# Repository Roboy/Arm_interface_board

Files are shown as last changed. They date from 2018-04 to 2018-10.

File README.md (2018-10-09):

# Arm_interface_board
Board containing all the control units and power distribution for the servos in the arms.

## Hardware Setup
1. Check and/or solder the clock crystal on the board. Bridge the appropiate pads in order to enable it or make use
  of the extra two pins.
2. Crimp the connectors for power/i2c and the servos according to the following diagram:
   - **Power/I2C:**\
      5V |||||| GND         ]\
      SDA|||||| blah        ] TODO
   - **Servos:**\
      The connectors on the board are designed to receive a connection that starting with the indexing pin on the left
      (to the right) look like this:
      - 5V
      - GND
      - SIGNAL\

   Be careful and rearrange the connections before crimping if needed. Also make sure the cables exit the connector in an
   appropiate direction, to avoid loops.

## Software and flashing guide
The board can be programmed with the Arduino IDE but some setup is required.
### For boards with the ATMEGA328PB
This is partially the result of a mistake in ordering the uControllers,
so the board is not actually designed to fit the chip. Even so it works without
much modifications, although one should exercise special care to **tristate** the pins
that are connected directly to power (A & B).
#### Prerequisites
- MCUdude's [MiniCore](https://github.com/MCUdude/MiniCore) (and all it's dependencies:)
- Arduino IDE v.1.6.4 or greater
#### Setup
You need to install extra packages to enable compatibility with this chip in
the Arduino IDE.\
Add the following URLs to the **Additional Boards Manager URLs**:
```
https://mcudude.github.io/MiniCore/package_MCUdude_MiniCore_index.json
```
This one enables and advanced bootloader and the extra functions in the PB series.
For this you also need the latest AVR toolchain (version 1.6.206). Add:
```
https://downloads.arduino.cc/packages/package_avr_3.6.0_index.json
```
to your Boards Manager.\

After you do this you can install the Minicore and update the Arduino AVR boards to
1.6.207 (AVR toolchain).
#### Flashing
To flash the board you need to use an ISP programmer. The easiest way is to use
an arduino as the programmer. You can do this by flashing any Arduino board with
the code from *Examples*>*11. ArduinoISP*>*ArduinoISP*. Afterwards you can select
the AVR chip from the Minicore boards and configure it for the specified clock, etc.
With all options set you can burn the bootloader by selecting "Arduino as ISP"
in the Programmer window.\

Sadly with this version of the AVR toolchain, for some reason the flashing does not work out of the box.
You require the latest version of **avrdude**, and the only way is by compiling
it from the [source](https://github.com/sigmike/avrdude).\
After you install it the flashing procedure is a bit different. You have to first
compile your code, and then using your freshly built avrdude version upload it
to your board.

UPDATE: downgrade to avr boards 1.6.23 and install arduino isp on atmega 2560. switch to 1.6.207 and install bootloader.

sudo ./avrdude -Cavrdude.conf -v -pm328p -cstk500v1 -P/dev/ttyACM0 -b19200 -D -Uflash:w:/tmp/arduino_build_XXXXXX/roboy_arm_board.ino.hex:i -F

in above command replace XXXXXX with your build number

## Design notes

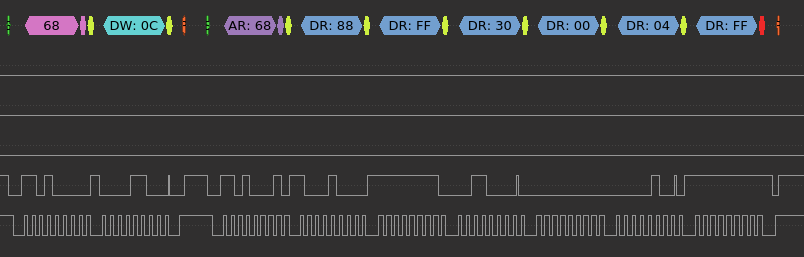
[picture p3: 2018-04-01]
roboy_arm_board/bmi160_IMU/i2cTrace.png

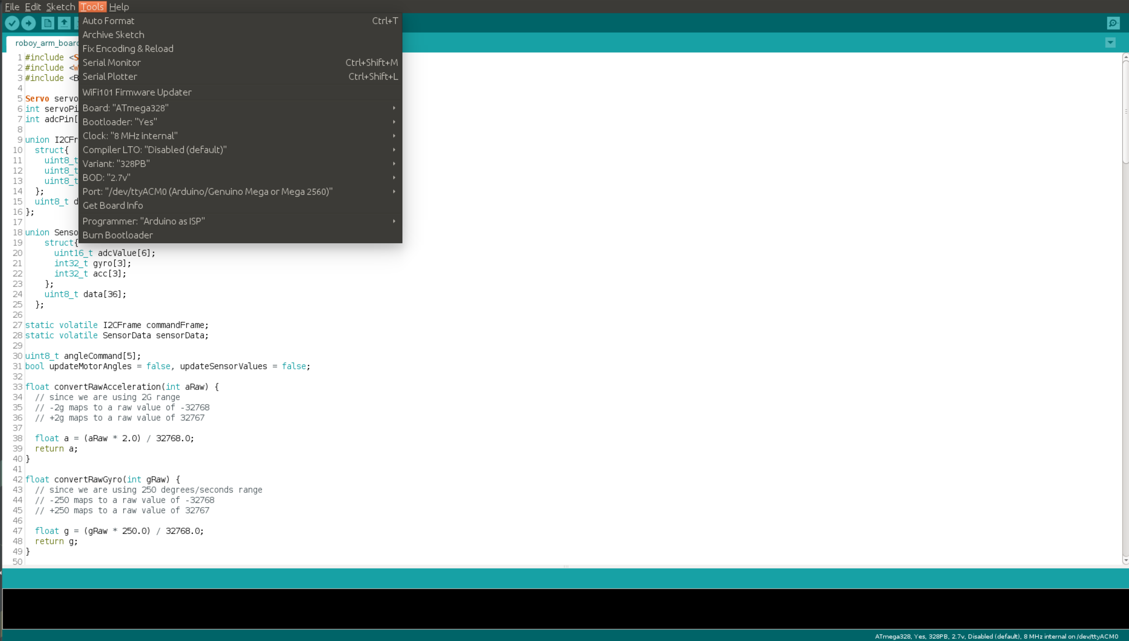
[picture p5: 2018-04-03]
roboy_arm_board/ArduinoConfigsForFlashingArmBoards.png

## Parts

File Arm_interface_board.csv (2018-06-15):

Id | Designator | Package | Quantity | Designation | Supplier and ref
1 | SW2 | SW_SPST_KXT3 | 1 | USER_SW
2 | MK3,MK2,MK1 | MountingHole_2.2mm_M2_DIN965_Pad | 3 | Mounting_Hole_PAD
3 | J19,J18,J16,J17,J20 | TE-Connectivity_Micro-Match_connector_02x02_Pitch_1.27mm | 5 | CONN_01X04
4 | J3 | PinHeader_2x03_P2.54mm_Vertical | 1 | ICSP
5 | U4 | TQFP-32_7x7mm_P0.8mm | 1 | ATMEGA328PB-AU
6 | Y1 | Crystal_SMD_TXC_7M-4Pin_3.2x2.5mm | 1 | TSX-3225 20MHz
7 | J6 | JST_S10B-PHDSS_2x05x2.00mm_Angled | 1 | JST_PHD_connector_02x05_angled_male
8 | C1,C3,C8,C9,C10,C11,C12,C13,C14,C15,C16 | C_0402_1005Metric | 11 | 100n
9 | C4,C5 | C_0402_1005Metric | 2 | 22p
10 | C6,C7 | C_0402_1005Metric | 2 | 1u
11 | S-IN1,Aref1,S1,S2,S3,S4,S5 | TestPoint_Pad_D1.0mm | 7 | TEST_1P
12 | JP1 | SolderJumper-3_P1.3mm_Open_RoundedPad1.0x1.5mm | 1 | XTAL_EN1
13 | JP2 | SolderJumper-3_P1.3mm_Open_RoundedPad1.0x1.5mm | 1 | XTAL_EN2
14 | R2,R9 | R_0402_1005Metric | 2 | 10k
15 | R3,R4,R5,R6,R7 | R_1206_3216Metric | 5 | 10mOhm
16 | SW1 | SW_SPST_SKQG | 1 | SW_Push
17 | U1,U7,U8,U9,U10,U11 | SOT-23-5 | 6 | INA180
18 | U3 | X2SON-8_1.4x1mm_P0.35mm | 1 | NTS0102
19 | U5 | SOT-23-5 | 1 | MIC5504-3.3YM5
20 | U2 | Bosch_LGA-14_3x2.5mm_P0.5mm | 1 | BMI160
21 | R1 | R_1206_3216Metric | 1 | 1mOhm
22 | C2 | CP_Elec_4x5.3 | 1 | 22u
23 | G*** | R1_face_mask_5.5mm | 1 | LOGO
24 | G*** | R1_eyes_mask_5.5mm | 1 | LOGO
25 | G*** | R1_ear_silk_5.5mm | 1 | LOGO
26 | D1 | LED_0603_1608Metric | 1 | LED
27 | R8 | R_0402_1005Metric | 1 | 1k
28 | G*** | Roboy_text_5.5mm | 1 | LOGO
29 | D2 | LED_0603_1608Metric | 1 | USER_LED(PB0)
30 | J1 | PinHeader_2x08_P1.27mm_Vertical | 1 | CONN_02X08

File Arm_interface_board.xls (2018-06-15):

Id | Designator | Package | Quantity | Designation | Supplier and ref
0 | SW2 | SW_SPST_KXT3 | 1 | USER_SW
1 | MK3,MK2,MK1 | MountingHole_2.2mm_M2_DIN965_Pad | 3 | Mounting_Hole_PAD
2 | J19,J18,J16,J17,J20 | TE-Connectivity_Micro-Match_connector_02x02_Pitch_1.27mm | 5 | CONN_01X04 | https://www.digikey.com/product-detail/en/te-connectivity-amp-connectors/215079-4/A107031CT-ND/3488592
3 | J3 | PinHeader_2x03_P2.54mm_Vertical | 1 | ICSP | Whatever, pins
4 | U4 | TQFP-32_7x7mm_P0.8mm | 1 | ATMEGA328-AU | https://www.digikey.com/product-detail/en/microchip-technology/ATMEGA328PB-AUR/ATMEGA328PB-AURCT-ND/5722706
5 | Y1 | Crystal_SMD_TXC_7M-4Pin_3.2x2.5mm | 1 | TSX-3225 20MHz | Some seiko, will update
6 | J6 | JST_S10B-PHDSS_2x05x2.00mm_Angled | 1 | JST_PHD_connector_02x05_angled_male | Also later update, already in stock
7 | C1,C3,C8,C9,C10,C11,C12,C13,C14,C15,C16 | C_0402_1005Metric | 11 | 100n
8 | C4,C5 | C_0402_1005Metric | 2 | 22p
9 | C6,C7 | C_0402_1005Metric | 2 | 1u
10 | S-IN1,Aref1,S1,S2,S3,S4,S5 | TestPoint_Pad_D1.0mm | 7 | TEST_1P
11 | J1 | PinHeader_2x08_P1.27mm_Vertical | 1 | CONN_02X08
12 | JP1 | SolderJumper-3_P1.3mm_Open_RoundedPad1.0x1.5mm | 1 | XTAL_EN1
13 | JP2 | SolderJumper-3_P1.3mm_Open_RoundedPad1.0x1.5mm | 1 | XTAL_EN2
14 | R2,R9 | R_0402_1005Metric | 1 | 10k
15 | R3,R4,R5,R6,R7,R1 | R_1206_3216Metric | 5 | 10mOhm | https://www.digikey.com/product-detail/en/te-connectivity-passive-product/RLP73V2BR010FTDF/A109621CT-ND/4032387
16 | SW1 | SW_SPST_SKQG | 1 | SW_Push | https://www.digikey.com/product-detail/en/e-switch/TL3305AF260QG/EG5353CT-ND/5816198
17 | U1,U7,U8,U9,U10,U11 | SOT-23-5 | 6 | INA180 | https://www.digikey.com/product-detail/en/texas-instruments/INA180A4IDBVR/296-47655-1-ND/8133024
18 | U3 | X2SON-8_1.4x1mm_P0.35mm | 1 | NTS0102 | https://www.digikey.com/product-detail/en/nxp-usa-inc/NTS0102GF115/568-5572-1-ND/2531050
19 | U5 | SOT-23-5 | 1 | MIC5504-3.3YM5 | https://www.digikey.com/product-detail/en/microchip-technology/MIC5504-3.3YM5-TR/576-4764-1-ND/4864028
20 | U2 | Bosch_LGA-14_3x2.5mm_P0.5mm | 1 | BMI160
21 | C2 | CP_Elec_4x5.3 | 1 | 22u | https://www.digikey.com/product-detail/en/panasonic-electronic-components/EEE-0JA220SR/PCE3857CT-ND/766233
22 | G*** | R1_face_mask_5.5mm | 1 | LOGO
23 | G*** | R1_eyes_mask_5.5mm | 1 | LOGO
24 | G*** | R1_ear_silk_5.5mm | 1 | LOGO
25 | D1 | LED_0603_1608Metric | 1 | LED | https://www.digikey.com/product-detail/en/lite-on-inc/LTST-C190KGKT/160-1435-1-ND/386814
26 | R8 | R_0402_1005Metric | 2 | 1k
27 | G*** | Roboy_text_5.5mm | 1 | LOGO
28 | R1 | R_1206_3216Metric | 1 | 2mOhm
29 | D2 | LED_0603_1608Metric | 1 | USER_LED(PB0)

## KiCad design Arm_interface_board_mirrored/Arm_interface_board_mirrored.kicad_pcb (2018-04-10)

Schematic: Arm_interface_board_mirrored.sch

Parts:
Aref1: TEST_1P; TestPoint_Pad_D1.0mm
C1, C3, C8, C9, C10, C11, C17: 100n; C_0402_1005Metric
C2: 22u; CP_Elec_4x5.3
C4, C5: 22p; C_0402_1005Metric
C6, C7: 1u; C_0402_1005Metric
D1: LED; LED_0603_1608Metric
D2: USER_LED(PB0); LED_0603_1608Metric
J1: CONN_02X08; PinHeader_2x08_P1.27mm_Vertical
J3: ICSP; PinHeader_2x03_P2.54mm_Vertical
J6: JST_PHD_connector_02x05_angled_male; JST_S10B-PHDSS_2x05x2.00mm_Angled
JP1: XTAL_EN1; SolderJumper-3_P1.3mm_Open_RoundedPad1.0x1.5mm
JP2: XTAL_EN2; SolderJumper-3_P1.3mm_Open_RoundedPad1.0x1.5mm
MK1, MK2, MK3: Mounting_Hole_PAD; MountingHole_2.2mm_M2_DIN965_Pad
R1: 1mOhm; R_1206_3216Metric
R2, R9: 10k; R_0402_1005Metric
R8: 1k; R_0402_1005Metric
S-IN1: TEST_1P; TestPoint_Pad_D1.0mm
SW1: SW_Push; SW_SPST_SKQG
SW2: USER_SW; SW_SPST_KXT3
U1: INA180; SOT-23-5
U2: BMI160; Bosch_LGA-14_3x2.5mm_P0.5mm
U3: NTS0102; X2SON-8_1.4x1mm_P0.35mm
U4: ATMEGA328PB-AU; TQFP-32_7x7mm_P0.8mm
U5: MIC5504-3.3YM5; SOT-23-5
Y1: TSX-3225 20MHz; Crystal_SMD_TXC_7M-4Pin_3.2x2.5mm

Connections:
+3V3: C7.1, C9.1, C10.1, J1.1, U2.5, U2.8, U2.12, U3.3, U3.6, U5.5
+5V: C1.1, C2.1, C3.1, C6.1, C17.1, J1.2, J3.2, R1.1, R2.1, R8.2, U1.4, U1.5, U3.7, U4.4 (VCC), U4.18 (AVCC), U5.1, U5.3; also elsewhere on the board
+5VP: J6.4, J6.6, J6.8, J6.10, R1.2, U1.3
/MISO: J1.7, J3.1, U4.16 ((MISO0/RXD1/PTCXY)PB4)
/MOSI: J1.5, J3.4, U4.15 ((MOSI0/TXD1/OC2A/PTCXY)PB3)
/PB0: R9.2, U4.12 ((CLKO/ICP1/PTCXY)PB0)
/PB6: J1.11, JP1.1
/PB7: J1.13, JP2.3
/PD0: J1.10, U4.30 ((RXD0/OC3A/PTCXY)PD0)
/PD1: J1.3, U4.31 ((TXD0/OC4A/PTCXY)PD1)
/PD2: J1.4, U4.32 ((OC3B/OC4B/INT0/PTCXY)PD2)
/PD4: SW2.1, U4.2 ((XCK0/T0/PTCXY)PD4)
/PD7: J1.12, U4.11 ((AIN1/PTCXY)PD7)
/RESET: C11.1, J3.5, R2.2, SW1.1, U4.29 ((~RESET~)PC6)
/SCK: J1.9, J3.3, U4.17 ((XCK0/SCK0/PTCXY)PB5)
/SCL: J1.16, J6.2, U4.28 ((SCL0/ADC5/PTCY)PC5)
/SCL1_H: U3.1, U4.6 (PE1(PTCXY/SCL1/T4))
/SCL1_L: J1.8, U2.13, U3.4
/SDA: J1.14, J6.1, U4.27 ((SDA0/ADC4/PTCY)PC4)
/SDA1_H: U3.8, U4.3 (PE0(PTCXY/SDA1/ICP4/ACO))
/SDA1_L: J1.6, U2.14, U3.5
/Servos/Current_adc1: U4.23 ((MISO1/ADC0/PTCY)PC0); also elsewhere on the board
/Servos/Current_adc2: U4.24 ((SCK1/ADC1/PTCY)PC1); also elsewhere on the board
/Servos/Current_adc3: U4.25 ((ADC2/PTCY)PC2); also elsewhere on the board
/Servos/Current_adc4: U4.26 ((ADC3/PTCY)PC3); also elsewhere on the board
/Servos/Current_adc5: U4.19 (PE2(PTCY/ADC6/ICP3/~SS1~)); also elsewhere on the board
/Servos/Servo_pwm1: U4.13 ((OC1A/PTCXY)PB1); also elsewhere on the board
/Servos/Servo_pwm2: U4.14 ((OC1B/~SS0~/PTCXY)PB2); also elsewhere on the board
/Servos/Servo_pwm3: U4.1 ((OC2B/INT1/PTCXY)PD3); also elsewhere on the board
/Servos/Servo_pwm4: U4.9 ((OC0B/T1/PTCXY)PD5); also elsewhere on the board
/Servos/Servo_pwm5: U4.10 ((OC0A/AIN0/PTCXY)PD6); also elsewhere on the board
GND: C1.2, C2.2, C3.2, C4.1, C5.1, C6.2, C7.2, C8.2, C9.2, C10.2, C11.2, C17.2, D1.1, D2.1, J1.15, J3.6, J6.3, J6.5, J6.7, J6.9, MK1.1, MK2.1, MK3.1, SW1.2, SW2.2, U1.2, U2.1, U2.6, U2.7, U3.2, U4.5 (GND), U4.21 (GND), U5.2, Y1.2, Y1.4; also elsewhere on the board
unnamed: Aref1.1, C8.1, U4.20 (AREF)
unnamed: C4.2, JP1.3, Y1.1
unnamed: C5.2, JP2.1, Y1.3
unnamed: D1.2, R8.1
unnamed: D2.2, R9.1
unnamed: JP1.2, U4.7 ((XTAL1/TOSC1)PB6)
unnamed: JP2.2, U4.8 ((XTAL2/TOSC2)PB7)
unnamed: S-IN1.1, U1.1, U4.22 (PE3(PTCY/ADC7/T3/MOSI1))

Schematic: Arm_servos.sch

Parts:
C12, C13, C14, C15, C16: 100n; C_0402_1005Metric
J16, J17, J18, J19, J20: CONN_01X04; TE-Connectivity_Micro-Match_connector_02x02_Pitch_1.27mm
R3, R4, R5, R6, R7: 10mOhm; R_1206_3216Metric
S1, S2, S3, S4, S5: TEST_1P; TestPoint_Pad_D1.0mm
U7, U8, U9, U10, U11: INA180; SOT-23-5

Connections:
+5V: C12.1, C13.1, C14.1, C15.1, C16.1, R3.2, R4.2, R5.2, R6.2, R7.2, U7.3, U7.5, U8.3, U8.5, U9.3, U9.5, U10.3, U10.5, U11.3, U11.5; also elsewhere on the board
/Servos/Current_adc1: S1.1, U7.1; also elsewhere on the board
/Servos/Current_adc2: S2.1, U8.1; also elsewhere on the board
/Servos/Current_adc3: S3.1, U9.1; also elsewhere on the board
/Servos/Current_adc4: S4.1, U10.1; also elsewhere on the board
/Servos/Current_adc5: S5.1, U11.1; also elsewhere on the board
/Servos/Servo_pwm1: J16.3; also elsewhere on the board
/Servos/Servo_pwm2: J17.3; also elsewhere on the board
/Servos/Servo_pwm3: J18.3; also elsewhere on the board
/Servos/Servo_pwm4: J19.3; also elsewhere on the board
/Servos/Servo_pwm5: J20.3; also elsewhere on the board
GND: C12.2, C13.2, C14.2, C15.2, C16.2, J16.2, J16.4, J17.2, J17.4, J18.2, J18.4, J19.2, J19.4, J20.2, J20.4, U7.2, U8.2, U9.2, U10.2, U11.2; also elsewhere on the board
unnamed: J16.1, R3.1, U7.4
unnamed: J17.1, R4.1, U8.4
unnamed: J18.1, R5.1, U9.4
unnamed: J19.1, R6.1, U10.4
unnamed: J20.1, R7.1, U11.4

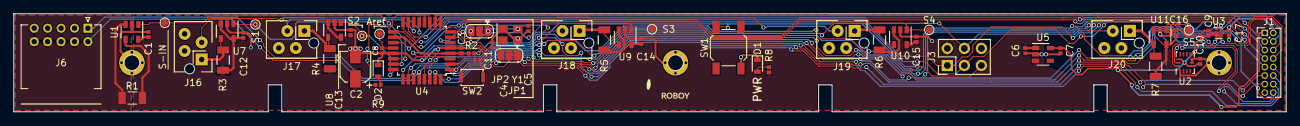
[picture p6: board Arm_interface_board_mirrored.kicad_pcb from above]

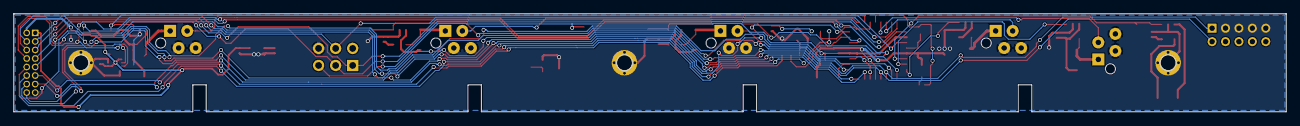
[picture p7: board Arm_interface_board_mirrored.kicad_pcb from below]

Board: 2 copper layers, 189.6 x 14.6 mm, 61 parts (3 on the bottom side), 45 nets.

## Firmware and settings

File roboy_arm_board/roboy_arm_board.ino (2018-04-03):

#include <Servo.h>
#include <Wire.h>
#include <BMI160Gen.h>

Servo servoMotor[5];
int servoPin[5] = {9, 10, 3, 5, 6};
int adcPin[5] = {14, 15, 16, 17, 18};

union I2CFrame{
  struct{
    uint8_t angleCommand[5] = {90,90,90,90,90};
    uint8_t servoControl;
    uint8_t gpioControl[5];
  };
  uint8_t data[11];
};

union SensorData{
    struct{
      uint16_t adcValue[6];
      int32_t gyro[3];
      int32_t acc[3];
    };
    uint8_t data[36];
  };

static volatile I2CFrame commandFrame;
static volatile SensorData sensorData;

uint8_t angleCommand[5];
bool updateMotorAngles = false, updateSensorValues = false;

float convertRawAcceleration(int aRaw) {
  // since we are using 2G range
  // -2g maps to a raw value of -32768
  // +2g maps to a raw value of 32767
  
  float a = (aRaw * 2.0) / 32768.0;
  return a;
}

float convertRawGyro(int gRaw) {
  // since we are using 250 degrees/seconds range
  // -250 maps to a raw value of -32768
  // +250 maps to a raw value of 32767
  
  float g = (gRaw * 250.0) / 32768.0;
  return g;
}

void InitADC()
{
    // Select Vref=AVcc
    ADMUX |= (1<<REFS0);
    //set prescaller to 128 and enable ADC 
    ADCSRA |= (1<<ADPS2)|(1<<ADPS1)|(1<<ADPS0)|(1<<ADEN);    
}

uint16_t ReadADC(uint8_t ADCchannel)
{
    //select ADC channel with safety mask
    ADMUX = (ADMUX & 0xF0) | (ADCchannel & 0x0F);
    //single conversion mode
    ADCSRA |= (1<<ADSC);
    // wait until ADC conversion is complete
    while( ADCSRA & (1<<ADSC) );
   return ADC;
}

void setup() {
  commandFrame.servoControl = 0xff;
  servoMotor[0].attach(servoPin[0]);
  servoMotor[1].attach(servoPin[1]);
  servoMotor[2].attach(servoPin[2]);
  servoMotor[3].attach(servoPin[3]);
  servoMotor[4].attach(servoPin[4]);

  Wire.begin(83);                // join i2c bus with address #8
  Wire.onReceive(receiveCommand); // register event
  Wire.onRequest(requestSensorData);

  pinMode(2, OUTPUT); 
  digitalWrite(2, HIGH);
  delay(200);
  digitalWrite(2, LOW);
  delay(200);
  digitalWrite(2, HIGH);
  delay(200);
  digitalWrite(2, LOW);
  delay(200);
  digitalWrite(2, HIGH);
  delay(200);
  digitalWrite(2, LOW);
  delay(200);

  InitADC();

  BMI160.begin(BMI160GenClass::I2C_MODE);
  BMI160.setGyroRate(25);
  BMI160.setGyroRange(25);
  BMI160.setAccelerometerRate(250);
  BMI160.setAccelerometerRange(2);
}

void loop() {
  if(updateMotorAngles){
    for(int motor = 0; motor<5; motor++)
      servoMotor[motor].write(commandFrame.angleCommand[motor]);
    updateMotorAngles = false;
  }

  for(int adc=0;adc<6;adc++){
    sensorData.adcValue[adc] = ReadADC(adc);
  }

  // read raw gyro measurements from device
  int gix, giy, giz, aix, aiy, aiz;
  BMI160.readGyro(gix,giy,giz);
  BMI160.readAccelerometer(aix,aiy,aiz);
//    float ax, ay, az, gx, gy, gz;
//    ax = convertRawAcceleration(aix);
//    ay = convertRawAcceleration(aiy);
//    az = convertRawAcceleration(aiz);
//    gx = convertRawGyro(gix);
//    gy = convertRawGyro(giy);
//    gz = convertRawGyro(giz);
    
  sensorData.gyro[0] = gix;
  sensorData.gyro[1] = giy;
  sensorData.gyro[2] = giz;

  sensorData.acc[0] = aix;
  sensorData.acc[1] = aiy;
  sensorData.acc[2] = aiz;
  
  delay(10);
}

static volatile int sensor_switch = 0;

void receiveCommand(int howMany) {
  uint8_t data[100];
  int byte_counter = 0;
  while (Wire.available()) { 
    data[byte_counter] = Wire.read(); // receive byte as a character
    byte_counter++;
  }
  uint8_t servoControl_backup = commandFrame.servoControl;
  switch(byte_counter){
    case 4:
      switch(data[0]){
        case 1:
          commandFrame.data[0] = data[3];
          commandFrame.data[1] = data[2];
          commandFrame.data[2] = data[1];
          digitalWrite(2, HIGH);
          break;
        case 2:
          commandFrame.data[3] = data[3];
          commandFrame.data[4] = data[2];
          commandFrame.data[5] = data[1];
          break;
        case 3:
          commandFrame.data[6] = data[3];
          commandFrame.data[7] = data[2];
          commandFrame.data[8] = data[1];
          break;
        case 4:
          commandFrame.data[9] = data[3];
          commandFrame.data[10] = data[2];
          updateMotorAngles = true;
          break;
      }
      if(updateMotorAngles){
        if(servoControl_backup!=commandFrame.servoControl){
          for(int motor=0;motor<5;motor++){
            if(commandFrame.servoControl!=0){
              servoMotor[motor].attach(servoPin[motor]);
            }else{
              servoMotor[motor].detach();
            }
//            if(commandFrame.servoControl&(0x1<<motor)){
//              servoMotor[motor].attach(servoPin[motor]);
//            }else{
//              servoMotor[motor].detach();
//            }
          }
        }
        
        digitalWrite(2, LOW);
      }
      break;
     case 1:
      sensor_switch = data[0];
      break;
  }
  
}

void requestSensorData() 
{ 
  switch(sensor_switch){
    case 0:
      Wire.write ((uint8_t*)sensorData.data, 12); 
    break;
    case 1:
      Wire.write ((uint8_t*)&sensorData.data[12], 12); 
    break;
    case 2:
      Wire.write ((uint8_t*)&sensorData.data[24], 12); 
    break;
  }
  
}

uint16_t adc_read(uint8_t adcx) {
  /* adcx is the analog pin we want to use.  ADMUX's first few bits are
   * the binary representations of the numbers of the pins so we can
   * just 'OR' the pin's number with ADMUX to select that pin.
   * We first zero the four bits by setting ADMUX equal to its higher
   * four bits. */
  ADMUX &=  0xf0;
  ADMUX |=  adcx;

  /* This starts the conversion. */
  ADCSRA |= _BV(ADSC);

  /* This is an idle loop that just wait around until the conversion
   * is finished.  It constantly checks ADCSRA's ADSC bit, which we just
   * set above, to see if it is still set.  This bit is automatically
   * reset (zeroed) when the conversion is ready so if we do this in
   * a loop the loop will just go until the conversion is ready. */
  while ( (ADCSRA & _BV(ADSC)) );

  /* Finally, we return the converted value to the calling function. */
  return ADC;
}

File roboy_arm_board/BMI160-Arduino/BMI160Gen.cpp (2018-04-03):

#define I2C_TIMEOUT 1000
#define I2C_PULLUP 1
#define SDA_PORT PORTD
#define SDA_PIN 0
#define SCL_PORT PORTD
#define SCL_PIN 1
#include <SoftI2CMaster.h>
#include "BMI160Gen.h"
#include "SPI.h"

//#define DEBUG

bool BMI160GenClass::begin(const int spi_cs_pin, const int intr_pin)
{
    return begin(SPI_MODE, spi_cs_pin, intr_pin);
}

bool BMI160GenClass::begin(Mode mode, const int arg1, const int arg2)
{
    this->mode = mode;
    switch (this->mode) {
    case INVALID_MODE:
        return false;
    case I2C_MODE:
        i2c_addr = arg1;
        break;
    case SPI_MODE:
        spi_ss = arg1;
        break;
    default:
        return false;
    }
    if (0 <= arg2) {
        interrupt_pin = digitalPinToInterrupt(arg2);
#ifdef DEBUG
        Serial.print("BMI160GenClass::begin(): pin#=");
        Serial.print(arg2);
        Serial.print(" -> interrupt=");
        Serial.println(interrupt_pin);
#endif
    }
    return CurieIMUClass::begin();
}

void BMI160GenClass::attachInterrupt(void (*callback)(void))
{
    CurieIMUClass::attachInterrupt(NULL);
    if (0 <= interrupt_pin) {
        ::attachInterrupt(interrupt_pin, callback, FALLING); 
    } else {
        Serial.println("BMI160GenClass::attachInterrupt: No valid interruption pin.");
    }
}

void BMI160GenClass::ss_init()
{
    switch (this->mode) {
    case I2C_MODE:
        i2c_init();
        break;
    case SPI_MODE:
        spi_init();
        break;
    default:
        break;
    }
}

int BMI160GenClass::ss_xfer(uint8_t *buf, unsigned tx_cnt, unsigned rx_cnt)
{
    switch (this->mode) {
    case I2C_MODE:
        return i2c_xfer(buf, tx_cnt, rx_cnt);
    case SPI_MODE:
        if (rx_cnt) /* For read transfers, assume 1st byte contains register address */
            buf[0] |= (1 << BMI160_SPI_READ_BIT);
        return spi_xfer(buf, tx_cnt, rx_cnt);
    default:
        return 0;
    }
}

void BMI160GenClass::i2c_init()
{
#ifdef DEBUG
  Serial.println("BMI160GenClass::i2c_init()...");
#endif // DEBUG
  //i2c_start_wait((i2c_addr<<1)|I2C_WRITE);
  //Wire.begin();
  //Wire.beginTransmission(i2c_addr);
  //if( Wire.endTransmission() != 0 )
  //    Serial.println("BMI160GenClass::i2c_init(): I2C failed.");

#ifdef DEBUG
  int id = getDeviceID();
  Serial.print("BMI160GenClass::i2c_init(): CHIP ID = 0x");
  Serial.println(id, HEX);
  Serial.println("BMI160GenClass::i2c_init()...done");
#endif // DEBUG
}

int BMI160GenClass::i2c_xfer(uint8_t *buf, unsigned tx_cnt, unsigned rx_cnt)
{
  uint8_t *p;

#ifdef DEBUG
  Serial.print("i2c_xfer(offs=0x");
  Serial.print(*buf, HEX);
  Serial.print(", tx=");
  Serial.print(tx_cnt);
  Serial.print(", rx=");
  Serial.print(rx_cnt);
  Serial.print("):");
#endif // DEBUG

    

    i2c_start_wait((i2c_addr<<1)|I2C_WRITE);
  //Wire.beginTransmission(i2c_addr);
  p = buf;
  while (0 < tx_cnt) {
    tx_cnt--;
    i2c_write(*p++);
    //Wire.write(*p++);
  }
  i2c_stop();
  //if( Wire.endTransmission() != 0 ) {
  //    Serial.println("Wire.endTransmission() failed.");
  //}
  if (0 < rx_cnt) {
    i2c_rep_start((i2c_addr<<1)|I2C_READ);
    //Wire.requestFrom(i2c_addr, rx_cnt);
    p = buf;
    while ( 0 < rx_cnt) {
      rx_cnt--;
#ifdef DEBUG
      if(rx_cnt>0){
          int t = *p++ = i2c_read(false);
          Serial.print(" ");
          Serial.print(t, HEX);
      }else{
          int t = *p++ = i2c_read(true);
          Serial.print(" ");
          Serial.print(t, HEX);
      }
#else
      if(rx_cnt>0){
          *p++ = i2c_read(false);
      }else{
          *p++ = i2c_read(true);
      }
#endif // DEBUG
    }
    
    i2c_stop();
  }

#ifdef DEBUG
  Serial.println("");
#endif // DEBUG

  return (0);
}

void BMI160GenClass::spi_init()
{
#ifdef DEBUG
  Serial.println("BMI160GenClass::spi_init()...");
#endif // DEBUG

  // start the SPI library:
  SPI.begin();
  if (0 <= spi_ss) {
    pinMode(spi_ss, OUTPUT);
  } else {
    Serial.println("BMI160GenClass::spi_init(): WARNING: No chip select pin specified.");
  }

#ifdef DEBUG
  Serial.println("BMI160GenClass::spi_init()...done");
#endif // DEBUG
}

int BMI160GenClass::spi_xfer(uint8_t *buf, unsigned tx_cnt, unsigned rx_cnt)
{
  uint8_t *p;

#ifdef DEBUG
  Serial.print("BMI160GenClass::spi_xfer(");
  Serial.print((unsigned long)buf, HEX);
  Serial.print("=");
  Serial.print(*buf, HEX);
  Serial.print(",");
  Serial.print(tx_cnt);
  Serial.print(",");
  Serial.print(rx_cnt);
  Serial.print("):");
#endif // DEBUG

  if (0 <= spi_ss)
    digitalWrite(spi_ss, LOW);
  p = buf;
  while (0 < tx_cnt) {
    tx_cnt--;
    SPI.transfer(*p++);
  }
  p = buf;
  while (0 < rx_cnt) {
    rx_cnt--;
#ifdef DEBUG
    int t = *p++ = SPI.transfer(0);
    Serial.print(" ");
    Serial.print(t, HEX);
#else
    *p++ = SPI.transfer(0);
#endif // DEBUG
  }
  if (0 <= spi_ss)
    digitalWrite(spi_ss, HIGH);

#ifdef DEBUG
  Serial.println("");
#endif // DEBUG

  return (0);
}

BMI160GenClass BMI160;

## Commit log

2017-07-06 Initial commit, added dxf drawings and started to create the connector footprints
    [Arm_interface_board.kicad_pcb, Arm_interface_board.sch]
2017-07-20 Random work on custom footprints
    [Arm_interface_board.kicad_pcb]
2018-01-15 Cleaned up board outline. Changed main uController to the Atmega328 in a 32 pin package.
    [Arm_interface_board.kicad_pcb, Arm_interface_board.sch]
2018-01-19 Partially finished the schematic and readied footprints. Basic uController infrastructure, and current sensing mechanism with shunts and amps.
    [Arm_interface_board.kicad_pcb, Arm_interface_board.sch]
2018-01-23 Switched to KiCad 5 and made some great progress. Also some minor corrections.
    [Arm_interface_board.kicad_pcb, Arm_interface_board.sch]
2018-01-31 After battling against track widths and mechanical aspects, routing is complete\!
    [Arm_interface_board.kicad_pcb, Arm_interface_board.sch]
2018-01-31 Forgot to add files. God since when has this been happening\?
    [Arm_interface_board-2018-01-22-07-41-01.sch, Arm_servos-2018-01-22-07-41-01.sch, Arm_servos.sch]
2018-02-03 Added Roboy logo and cleaned silkscreen
    [Arm_interface_board.kicad_pcb, Arm_interface_panel.kicad_pcb]
2018-04-01 with communication fpga i2c and imu readout using bitbang
    [Arm_interface_board_mirrored.kicad_pcb]
2018-04-01 with correct imu readout hand
    [roboy_arm_board.ino]
2018-04-03 with arduino config
2018-04-03 with soft i2c version
2018-04-08 Finished the fixes that make the board fully compatible with the PB variant of the Atmega328 chip. Also added an user LED and button. Started mirroring the board manually for the other arm
    [Arm_interface_board.csv, Arm_interface_board.kicad_pcb, Arm_interface_board.xls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]
2018-04-08 Some more work on the mirrored board
    [Arm_interface_board_mirrored.kicad_pcb]
2018-04-10 Finished! The mirrored board is finished!
    [Arm_interface_board_mirrored.kicad_pcb, Arm_interface_board_mirrored.sch]
2018-04-10 Cleaned up a bit and started the panel
    [Arm_interface_board-B.Cu.gbl, Arm_interface_board-B.Mask.gbs, Arm_interface_board-B.Paste.gbp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]
2018-04-10 Finished the panel, boards now ready to be ordered.
    [Arm_interface_board_panel-B.Cu.gbl, Arm_interface_board_panel-B.Mask.gbs, Arm_interface_board_panel-B.Paste.gbp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]
2018-04-10 Cleaned up old panel files and zipped the new ones.
    [Arm_interface_panel-B.Cu.gbl, Arm_interface_panel-B.Mask.gbs, Arm_interface_panel-B.Paste.gbp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]
2018-04-10 Felt too fancy and exported the gerbers with extended atributes enabled. Of course the people @ PCBWAY couldn't open them -.- .
    [Arm_interface_board_panel-B.Cu.gbl, Arm_interface_board_panel-B.Mask.gbs, Arm_interface_board_panel-B.Paste.gbp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]
2018-06-15 Updated BOM.
    [Arm_interface_board.csv, Arm_interface_board.xls]
